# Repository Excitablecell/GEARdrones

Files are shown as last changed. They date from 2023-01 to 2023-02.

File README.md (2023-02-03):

# GEARdrones

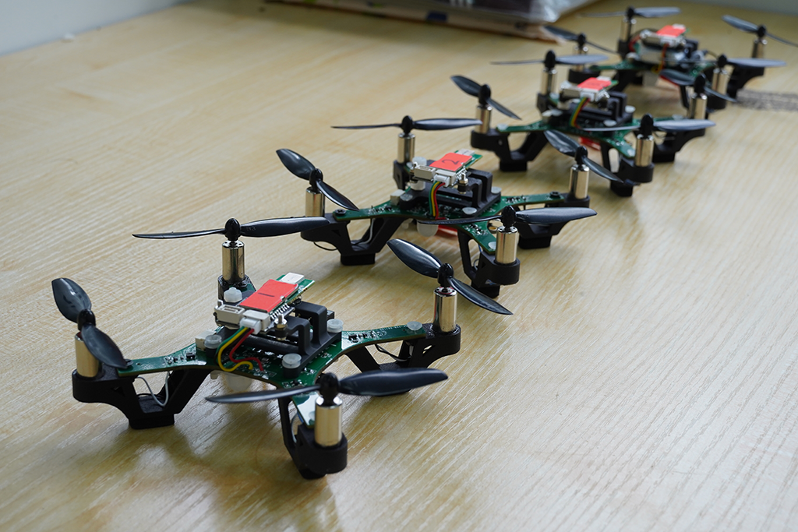
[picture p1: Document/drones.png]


> GEARdrones是一个专为**低成本无人机编队控制**所开发的，集**飞行控制器**、**UWB相对定位算法**、**软件上位机**于一体的四旋翼无人机系统。
>
> 演示视频：[自研无人机集群？理工男的大学生活也可以很精彩！](https://www.bilibili.com/video/BV1JY4y1o76U)
>
> 本项目主要包含以下内容：
>
> 	1.基于STM32F1和F4的两个版本的飞行控制器嵌入式软件工程
>
> 	2.基于STM32F1的遥控器嵌入式软件工程
>
> 	3.无人机的PCB工程(正在整理)、外壳模型
>
> 	4.相对定位算法的Matlab仿真文件
>
> 	5.基于PYQT5和MQTT开发的软件上位机

### 参考开发环境：

	嵌入式软件开发环境：Keil MDK5 5.29

	编译器：Arm Compiler V5.06 build750

	MQTT服务器：mosquito/EMQX

	MATLAB 2022B

	Python 3.8

### 参考文献：

> [1] Guo K, Xie L. INFRASTRUCTURE-FREE COOPERATIVE RELATIVE LOCALIZATION FOR UAVS IN GPS-DENIED ENVIRONMENTS[J]. International Journal of Robotics and Automation, 2021, 36(6).
>
> [2] Nguyen T M, Zaini A H, Guo K, et al. An ultra-wideband-based multi-UAV localization system in GPS-denied environments[C]//2016 International Micro Air Vehicles Conference. 2016, 6: 1-15.
>
> [3] Guo K, Qiu Z, Miao C, et al. Ultra-wideband-based localization for quadcopter navigation[J]. Unmanned Systems, 2016, 4(01): 23-34.
>
> [4] Guo K, Li X, Xie L. Ultra-wideband and odometry-based cooperative relative localization with application to multi-UAV formation control[J]. IEEE transactions on cybernetics, 2019, 50(6): 2590-2603.

### 参考开源库：

[SRML:华南虎嵌入式软件中间件层库](https://github.com/scutrobotlab/srml)

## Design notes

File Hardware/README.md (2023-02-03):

注意：PCB工程使用Altium Designer设计，使用其他EDA可能存在不兼容问题

所开源的PCB包含以下内容：

GEARdrones-Lite 原理图、PCB与BOM表

GEARdrones-F4 原理图、PCB

由于个人精力和开发周期的原因，F4版本的硬件方案仅用于测试分布式UWB相对定位算法，飞行功能没有被验证，本次开源也只是提供参考思路，具体原因可查阅：https://github.com/Excitablecell/GEARdrones/tree/main/Firmware

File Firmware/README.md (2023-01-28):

# GEARDRONE_LITE

GEARdrone for STM32F103

GEARdrone_Lite包含了完整的飞行控制器和机载UWB相对定位算法，可以在4基站模式下实现相对定位，或直接使用光流传感器进行定位悬停。

具体功能请查阅软件工程代码

# GEARDRONE_F4

 GEARdrone for STM32F411

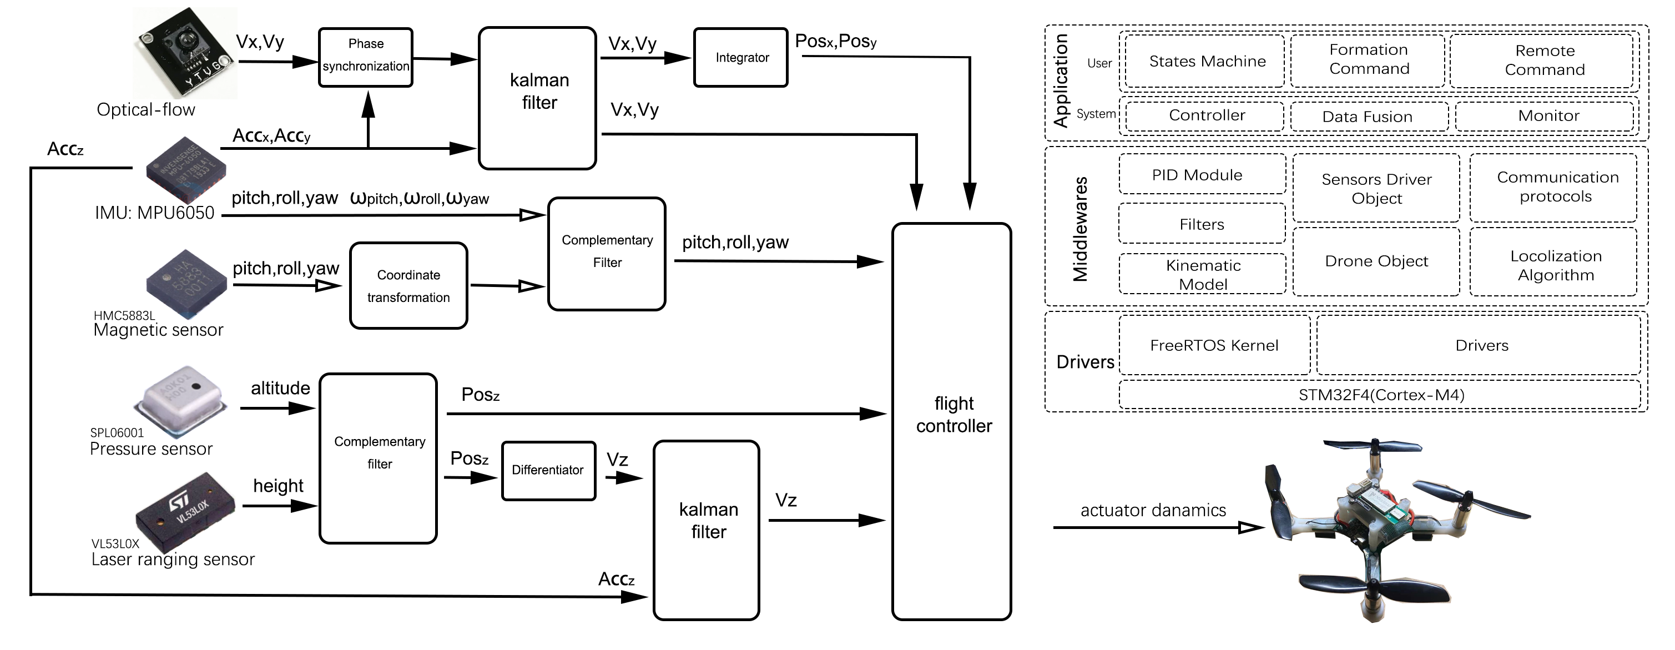
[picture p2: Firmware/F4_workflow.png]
F4 system workflow


F4版本飞控由于本人精力有限，在数次因layout问题打样测试失败后已暂停开发

值得参考的内容是 GEARdrone-F4\GearLL\Middlewares\Algorithm 目录下的 NLR_localization 文件

NLR_localization在单片机中实现非线性回归，复现了参考文献[1]中的第一部分无人机相对位置初始化部分的内容

完整论文复现的matlab仿真可以在software文件夹中查阅。

# GEARREMOTE

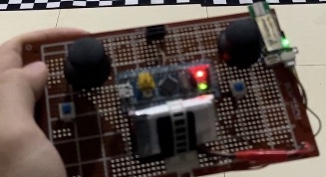
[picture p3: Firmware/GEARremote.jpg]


遥控器GEARremote原本是为了控制单独一架无人机设计的，使用串口透传模块进行通讯。但在后期编队开发中，为了下达广播起飞指令，遥控器摒弃了原先的设计，一直以面包板的形式支持无人机编队的开发，没有专门的PCB工程。

参考文献：

[1] Guo K, Xie L. INFRASTRUCTURE-FREE COOPERATIVE RELATIVE LOCALIZATION FOR UAVS IN GPS-DENIED ENVIRONMENTS[J]. International Journal of Robotics and Automation, 2021, 36(6).

[2] Nguyen T M, Zaini A H, Guo K, et al. An ultra-wideband-based multi-UAV localization system in GPS-denied environments[C]//2016 International Micro Air Vehicles Conference. 2016, 6: 1-15.

[3] Guo K, Qiu Z, Miao C, et al. Ultra-wideband-based localization for quadcopter navigation[J]. Unmanned Systems, 2016, 4(01): 23-34.

[4] Guo K, Li X, Xie L. Ultra-wideband and odometry-based cooperative relative localization with application to multi-UAV formation control[J]. IEEE transactions on cybernetics, 2019, 50(6): 2590-2603.

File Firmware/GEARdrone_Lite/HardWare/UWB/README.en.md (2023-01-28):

[简体中文](./README.md) | English

<h1 align="center">NLink Unpack</h1>

<div align="center">



NLink Unpack is used for products of Nooploop，like [LinkTrack](https://www.nooploop.com/)，[LinkTrack AOA](http://www.nooploop.com/linktrack-aoa)，[TOFSense](https://www.nooploop.com/tofsense.Written in pure C language, can be used for building protocol parsing code

 

</div>

## Notice

- In case of compilation errors, make sure the compiler has turned on C99 support
- NLink protocol data follows the Little-Endian mode, this example code runs in the mode too, and the Big-Endian mode is not supported
- For variable length protocols, such as NLink_LinkTrack_NodeFrame1, heap memory allocation is used for dynamic nodes. If there are many nodes, please ensure enough heap space

## Usage

Refer to [example.c](./example.c) to get start

## License

The source code is released under a [BSD 3-Clause license](LICENSE).

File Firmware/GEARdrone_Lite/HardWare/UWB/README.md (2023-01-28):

简体中文 | [English](./README.en.md) 

<h1 align="center">NLink Unpack</h1>

<div align="center">



NLink Unpack 用于支持Nooploop产品，如[LinkTrack](https://www.nooploop.com/)，[LinkTrack AOA](http://www.nooploop.com/linktrack-aoa)，[TOFSense](https://www.nooploop.com/tofsense)，纯C语言编写，用户可用于构建协议解析代码

 

</div>

## Notice
- 如编译错误，请确保编译器已经开启C99支持
- NLink协议数据遵循小端模式，本示例代码默认运行于小端模式，大端模式不可用
- 对于变长协议，如NLink_LinkTrack_NodeFrame1，动态节点部分采用了堆内存分配，如节点数量较多，请确保堆空间足够

## Usage

使用示例参考[example.c](./example.c)文件

## License

源码基于[BSD 3-Clause license](LICENSE)发布

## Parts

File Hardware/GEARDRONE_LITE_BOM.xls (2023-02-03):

型号 | 封装 | 位号 | 元件编号
0.22uf | 0603_C | C25 | C21120
22pF | C0603 | C10 | C1653
SS14 | SOD-323 | D4,D3,D2,D5,D1 | C699102
106 | C0603 | C5 | C96446
4.7uf | 0603_C | C24 | C19666
104 | C0603 | C14,C13,C7,C4,C16,C15,C3,C8,C6 | C14663
104 | 0603_C | C27,C26,C12,C11 | C14663
0.1uf | C0603 | C23,C22 | C14663
10nf | C0603 | C2 | C57112
10k | R0603 | R20,R19,R8,R6,R3,R33,R2,R1,R9 | C25804
10kΩ | R0603 | R10 | C25804
10k | 0603_R | R7,R11 | C25804
100k | R0603 | R30 | C25803
QMC5883L | LPCC-16_L3.0-W3.0-P0.50-BL | U4 | C976032
0 | R0603 | R5,R4 | C21189
SI2302 | LC-SOT-23(SOT-23-3) | Q5,Q4,Q3,Q2,Q1 | C2891732
73.2k | R0603 | R31 | C403343
5032 | SMD5032-2 | Y1 | C115962
STM32F103C8T6 | LC-LQFP-48_7X7X05P | U1 | C8734
4.7uH | CD43NP | L1 | C57269
2.2nf | C0603 | C1 | C1604
20pf | C0603 | C9 | C1648
SM04B-GHS-TB(LF)(SN) | CONN-SMD_4P-P1.25_SM04B-GHS-TB-LF-SN | U3 | C189895
EFD3-G9CA-P1WF | LED3528 | LED1 | C507038
SPL06-001 | SENSOR-SMD_SPL06-001 | U5 | C2684428
15pf | C0603 | C19 | C1644
ESP-12F(ESP8266MOD) | WIFIM-SMD_ESP-12F-ESP8266MOD | U2 | C82891
22uf | C0603 | C18,C17 | C59461
AMS1117-3.3 | LC-SOT-223 | T1 | C6186
SX1308 | LC-SOT-23-6 | IC2 | C78162
ECAP | TAN-A-3216 | C21,C20 | C7171

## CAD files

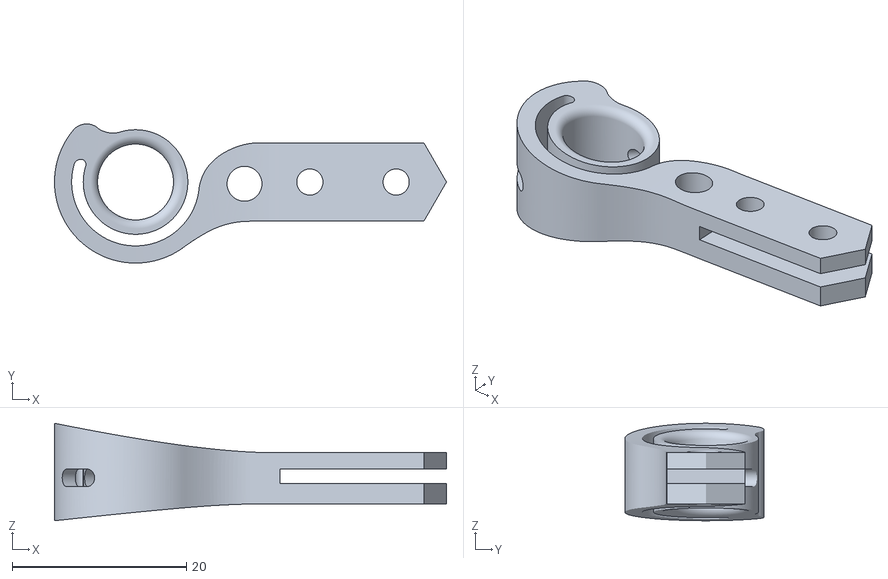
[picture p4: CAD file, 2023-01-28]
Model/GEARdrone_F4/Motor_holder_right.stl
45.0 x 16.0 x 11.2

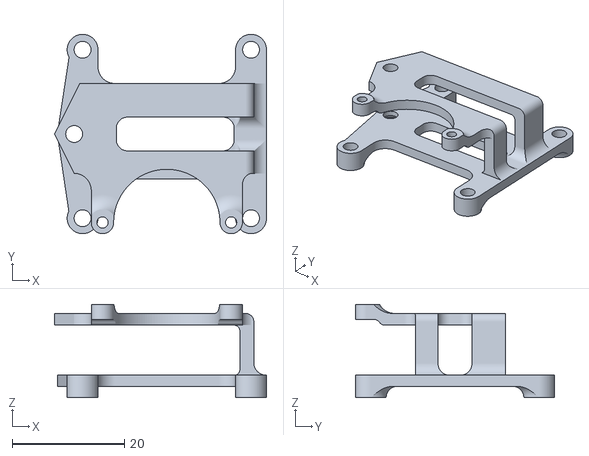
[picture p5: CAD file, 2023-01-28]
Model/GEARdrone_Lite/Upper_structure.stl
37.7 x 35.5 x 16.6

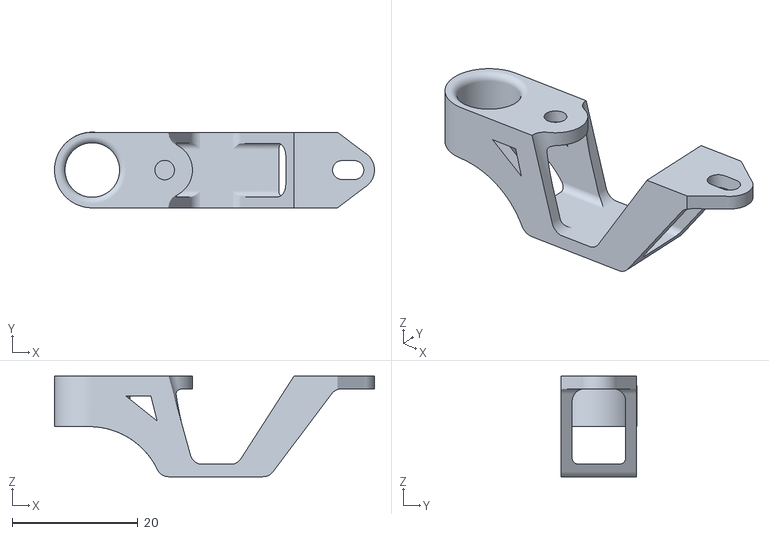
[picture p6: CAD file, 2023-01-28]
Model/GEARdrone_Lite/Motor_structure.stl
50.8 x 12.0 x 16.0

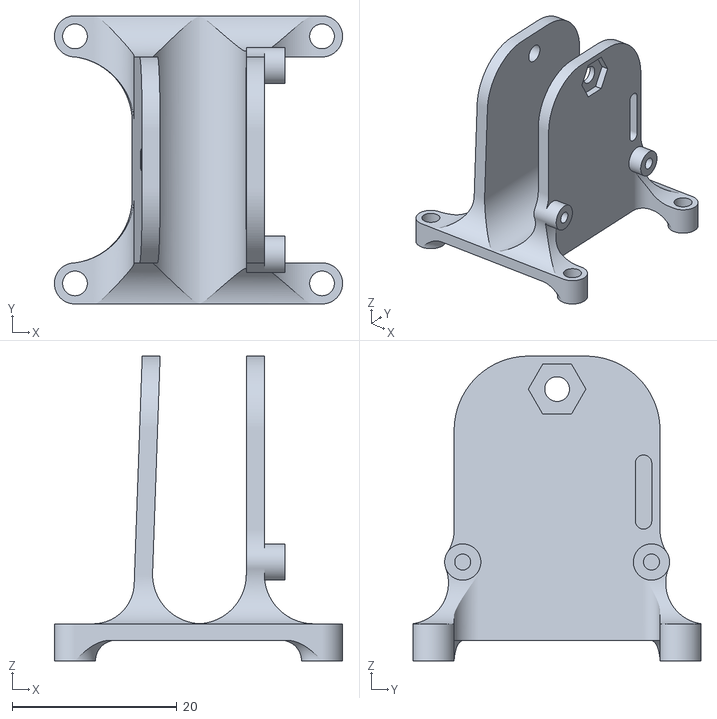
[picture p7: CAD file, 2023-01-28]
Model/GEARdrone_F4/Battery_holder.stl
35.0 x 35.0 x 37.0

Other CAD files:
Model/GEARdrone_F4/Motor_holder_left.stl

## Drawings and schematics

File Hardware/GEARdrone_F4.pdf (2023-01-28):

# stm32最小系统 MPU6050

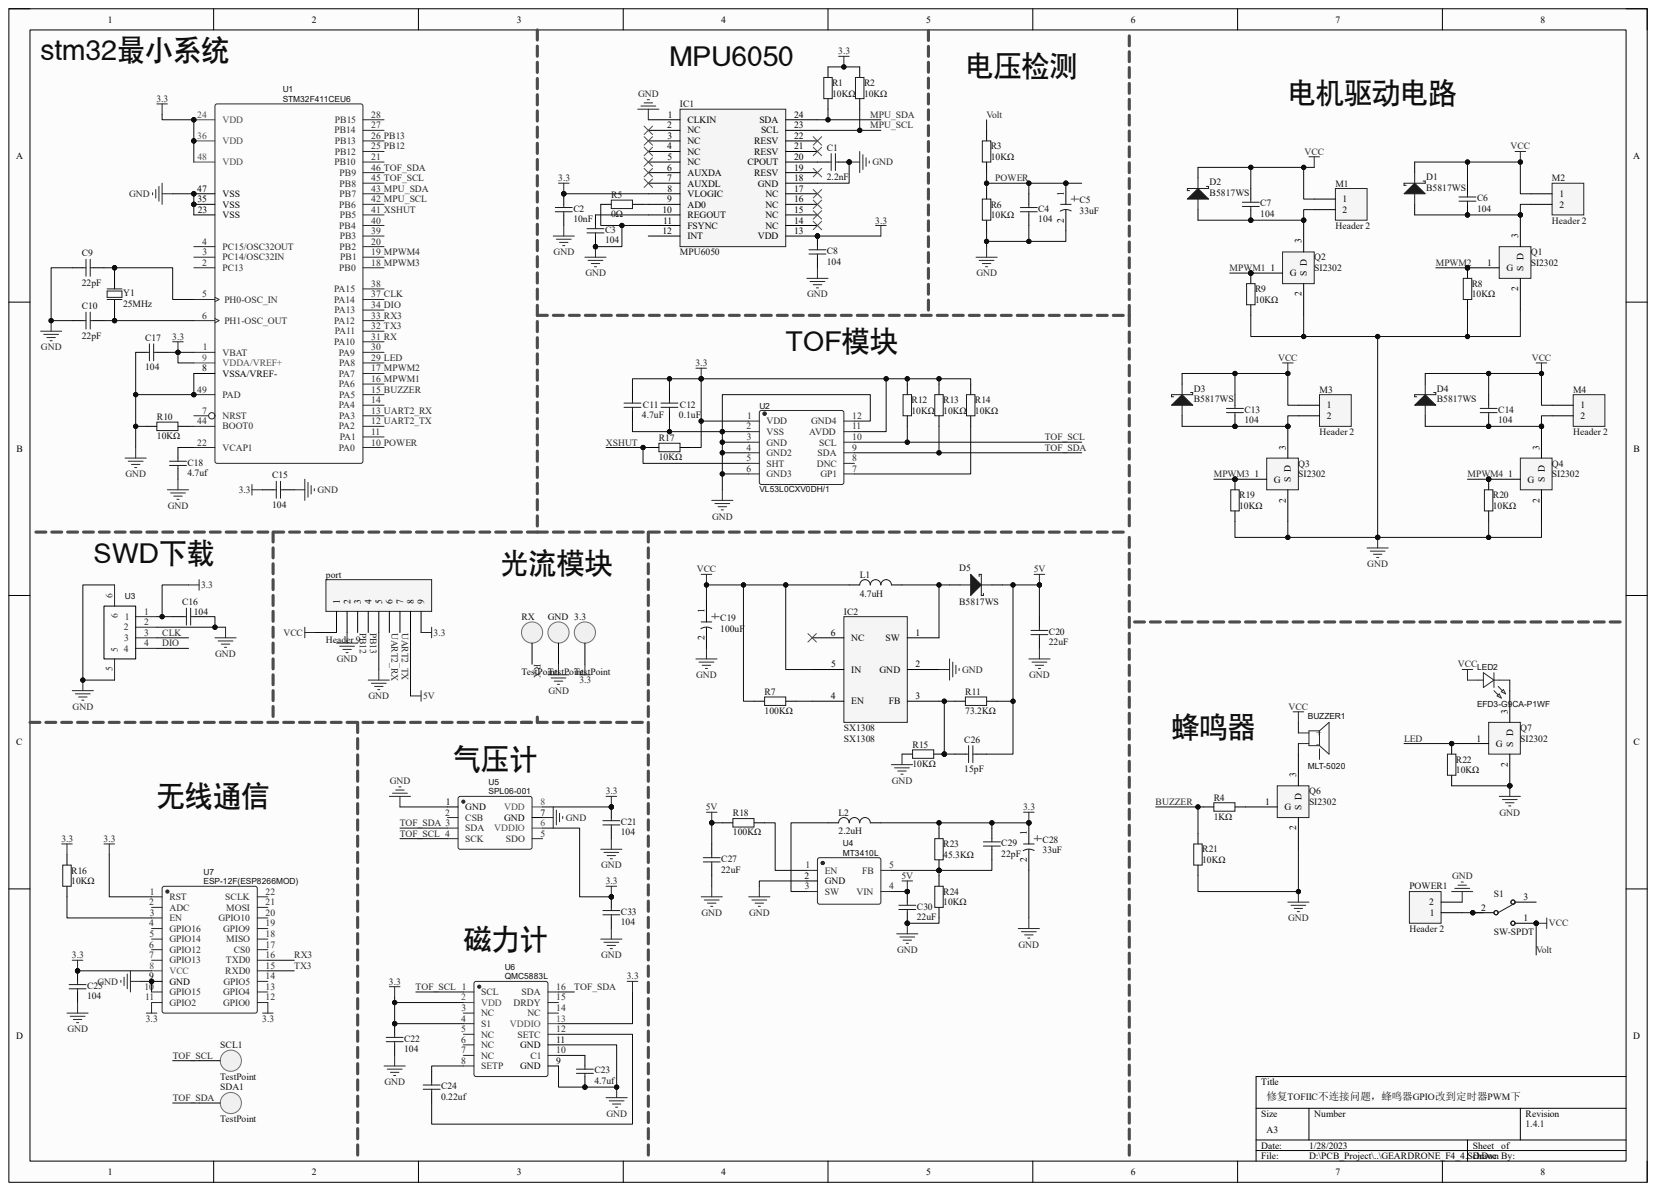
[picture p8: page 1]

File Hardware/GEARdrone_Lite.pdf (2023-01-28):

# stm32最小系统 MPU6050

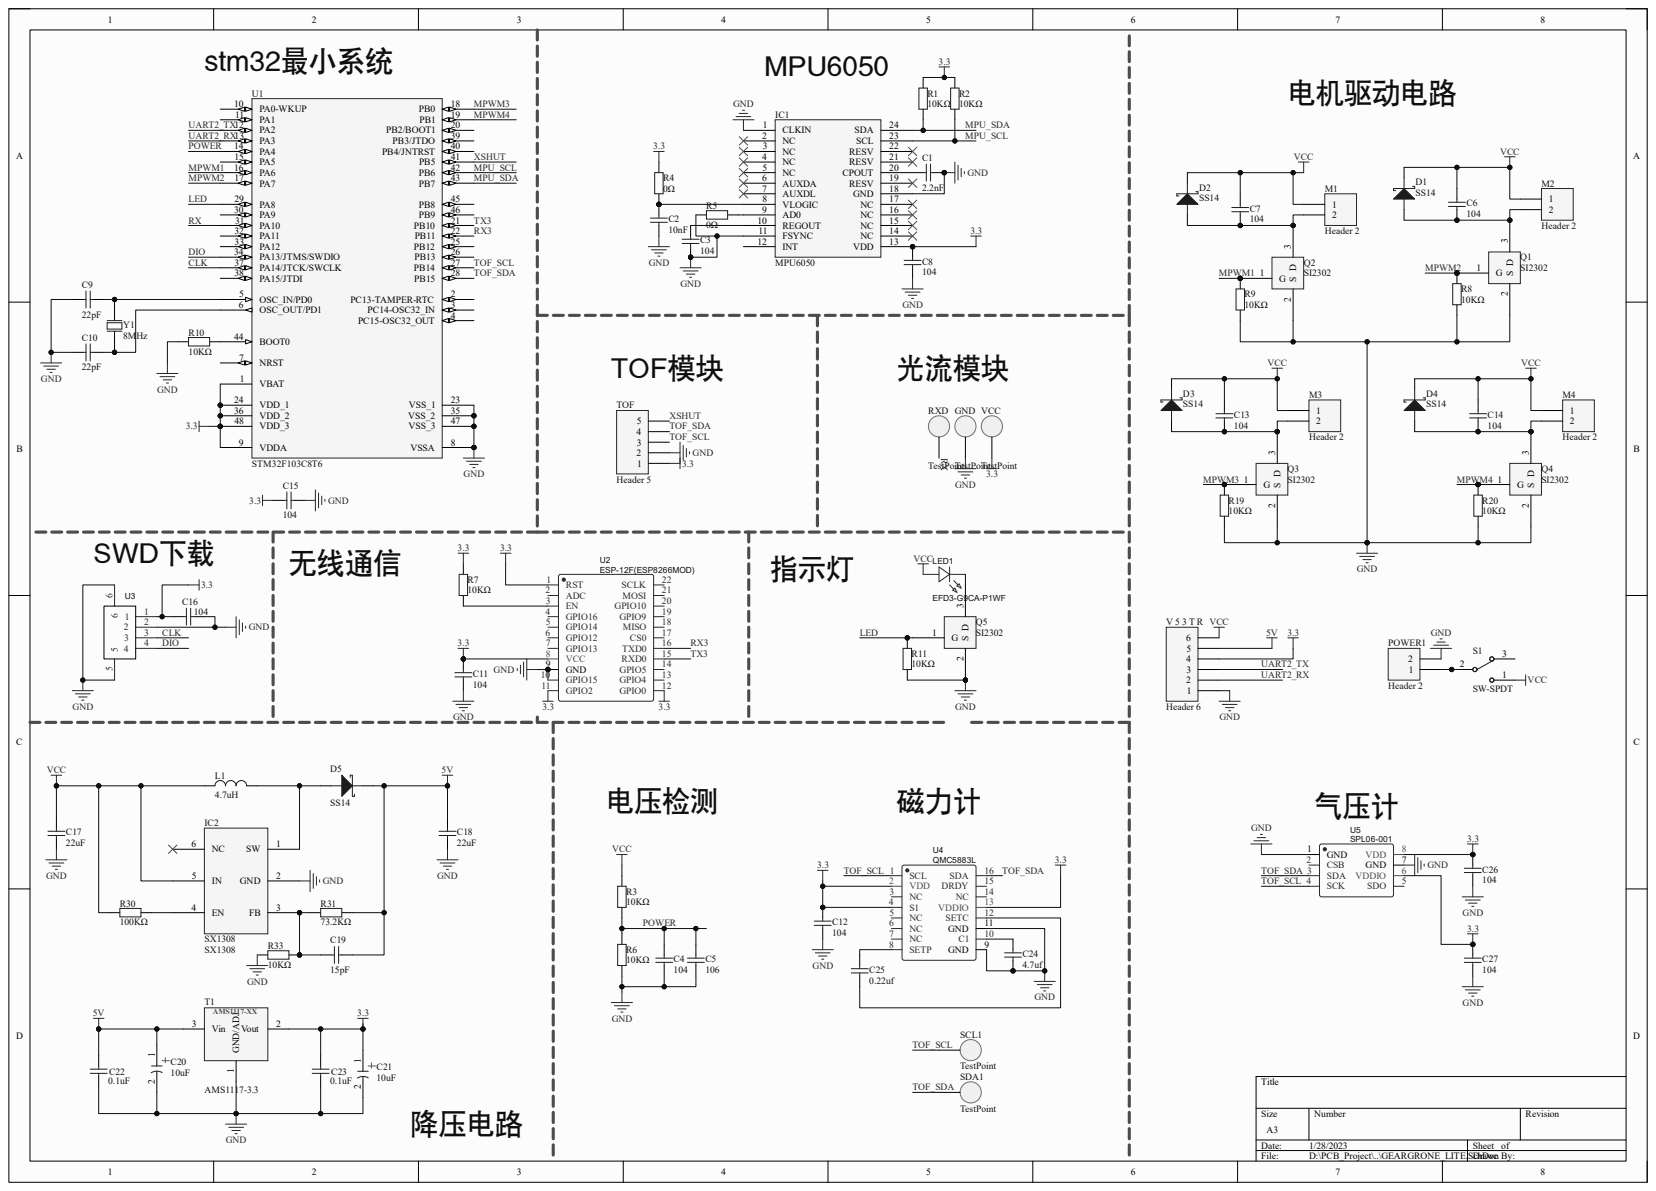
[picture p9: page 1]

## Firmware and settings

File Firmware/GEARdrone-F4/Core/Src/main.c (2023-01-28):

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
/* Includes ------------------------------------------------------------------*/
#include "main.h"
#include "cmsis_os.h"

/* USER CODE BEGIN Includes */
#include "SEGGER_SYSVIEW.h"
#include "inv_mpu.h"
#include "mpu6050.h"
#include "timer_driver.h"
/* USER CODE END Includes */

ADC_HandleTypeDef hadc1;
DMA_HandleTypeDef hdma_adc1;

I2C_HandleTypeDef hi2c1;

TIM_HandleTypeDef htim3;
TIM_HandleTypeDef htim4;
TIM_HandleTypeDef htim5;

UART_HandleTypeDef huart1;
UART_HandleTypeDef huart2;
UART_HandleTypeDef huart6;
DMA_HandleTypeDef hdma_usart1_rx;
DMA_HandleTypeDef hdma_usart1_tx;
DMA_HandleTypeDef hdma_usart2_tx;
DMA_HandleTypeDef hdma_usart2_rx;
DMA_HandleTypeDef hdma_usart6_rx;
DMA_HandleTypeDef hdma_usart6_tx;

osThreadId defaultTaskHandle;
void SystemClock_Config(void);
static void MX_GPIO_Init(void);
static void MX_DMA_Init(void);
static void MX_ADC1_Init(void);
static void MX_TIM3_Init(void);
static void MX_USART1_UART_Init(void);
static void MX_USART2_UART_Init(void);
static void MX_USART6_UART_Init(void);
static void MX_TIM4_Init(void);
static void MX_TIM5_Init(void);
static void MX_I2C1_Init(void);
void StartDefaultTask(void const * argument);

/* USER CODE BEGIN 0 */
#pragma import(__use_no_semihosting)
//标准库需要的支持函数
struct __FILE 
{
  int handle; 
};

FILE __stdout;
//定义_sys_exit()以避免使用半主机模式  
void _sys_exit(int x){x = x;}
void _ttywrch(int ch){ch = ch;}
	
//重定义fputc函数
int fputc(int ch, FILE *f){
  HAL_UART_Transmit(&huart6, (uint8_t *)&ch,1,0xff);  //根据使用的库重定向
  return ch;
}
uint8_t _dbg_TXBuff[20];
void uart2_printf(const char *format,...)
{
	uint32_t length;
	va_list args;

	va_start(args, format);
	length = vsnprintf((char*)_dbg_TXBuff, sizeof(_dbg_TXBuff)+1, (char*)format, args);
	va_end(args);
	HAL_UART_Transmit(&huart2,_dbg_TXBuff,length,0xff);
}
/* USER CODE END 0 */

/**
  * @brief  The application entry point.
  * @retval int
  */
int main(void)
{
  /* MCU Configuration--------------------------------------------------------*/

  /* Reset of all peripherals, Initializes the Flash interface and the Systick. */
  HAL_Init();

  /* Configure the system clock */
  SystemClock_Config();

  /* Initialize all configured peripherals */
  MX_GPIO_Init();
  MX_DMA_Init();
  MX_ADC1_Init();
  MX_TIM3_Init();
  MX_USART1_UART_Init();
  MX_USART2_UART_Init();
  MX_USART6_UART_Init();
  MX_TIM4_Init();
  MX_TIM5_Init();
  MX_I2C1_Init();
  /* USER CODE BEGIN 2 */
	System_Task_Init();
	SEGGER_SYSVIEW_Conf();
  /* USER CODE END 2 */

  /* USER CODE BEGIN RTOS_MUTEX */
  /* add mutexes, ... */
  /* USER CODE END RTOS_MUTEX */

  /* USER CODE BEGIN RTOS_SEMAPHORES */
  /* add semaphores, ... */
  /* USER CODE END RTOS_SEMAPHORES */

  /* USER CODE BEGIN RTOS_TIMERS */
  /* start timers, add new ones, ... */
  /* USER CODE END RTOS_TIMERS */

  /* USER CODE BEGIN RTOS_QUEUES */
  /* add queues, ... */
  /* USER CODE END RTOS_QUEUES */

  /* Create the thread(s) */
  /* definition and creation of defaultTask */
  osThreadDef(defaultTask, StartDefaultTask, osPriorityNormal, 0, 128);
  defaultTaskHandle = osThreadCreate(osThread(defaultTask), NULL);

  /* USER CODE BEGIN RTOS_THREADS */
  /* add threads, ... */
  /* USER CODE END RTOS_THREADS */

  /* Start scheduler */
  osKernelStart();

  /* We should never get here as control is now taken by the scheduler */
  /* Infinite loop */
  /* USER CODE BEGIN WHILE */
  while (1)
  {
    /* USER CODE END WHILE */

    /* USER CODE BEGIN 3 */
  }
  /* USER CODE END 3 */
}

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
/* USER CODE BEGIN Header_StartDefaultTask */
/**
  * @brief  Function implementing the defaultTask thread.
  * @param  argument: Not used
  * @retval None
  */
/* USER CODE END Header_StartDefaultTask */
void StartDefaultTask(void const * argument)
{
  /* USER CODE BEGIN 5 */
  /* Infinite loop */
  for(;;)
  {
		System_time_us = Get_SystemTimer();
    osDelay(1);

  }
  /* USER CODE END 5 */
}

/**
  * @brief  Period elapsed callback in non blocking mode
  * @note   This function is called  when TIM11 interrupt took place, inside
  * HAL_TIM_IRQHandler(). It makes a direct call to HAL_IncTick() to increment
  * a global variable "uwTick" used as application time base.
  * @param  htim : TIM handle
  * @retval None
  */
void HAL_TIM_PeriodElapsedCallback(TIM_HandleTypeDef *htim)
{
  /* USER CODE BEGIN Callback 0 */
	if (htim->Instance == TIM5) {
    Update_SystemTick();
  }
  /* USER CODE END Callback 0 */
  if (htim->Instance == TIM11) {
    HAL_IncTick();
  }
}

/**
  * @brief  This function is executed in case of error occurrence.
  * @retval None
  */
void Error_Handler(void)
{
  /* USER CODE BEGIN Error_Handler_Debug */
  /* User can add his own implementation to report the HAL error return state */
  __disable_irq();
  while (1)
  {
  }
  /* USER CODE END Error_Handler_Debug */
}

#ifdef  USE_FULL_ASSERT
/**
  * @brief  Reports the name of the source file and the source line number
  *         where the assert_param error has occurred.
  * @param  file: pointer to the source file name
  * @param  line: assert_param error line source number
  * @retval None
  */
void assert_failed(uint8_t *file, uint32_t line)
{
  /* USER CODE BEGIN 6 */
  /* User can add his own implementation to report the file name and line number,
     ex: printf("Wrong parameters value: file %s on line %d\r\n", file, line) */
  /* USER CODE END 6 */
}
#endif /* USE_FULL_ASSERT */

/************************ (C) COPYRIGHT STMicroelectronics *****END OF FILE****/

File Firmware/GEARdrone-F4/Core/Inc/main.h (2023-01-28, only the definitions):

#define ESPEN_Pin GPIO_PIN_12
#define ESPEN_GPIO_Port GPIOB
#define BEEP_Pin GPIO_PIN_15
#define BEEP_GPIO_Port GPIOB
#define LED_Pin GPIO_PIN_8
#define LED_GPIO_Port GPIOA
#define XSHUT_Pin GPIO_PIN_5
#define XSHUT_GPIO_Port GPIOB
#define TOF_SCL_Pin GPIO_PIN_8
#define TOF_SCL_GPIO_Port GPIOB
#define TOF_SDA_Pin GPIO_PIN_9
#define TOF_SDA_GPIO_Port GPIOB

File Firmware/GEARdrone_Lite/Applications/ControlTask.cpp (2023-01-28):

/********************************************************************************
  * Copyright (c) 2022 - ~, EXcai(亢体造梦)
  * @author  EXcai
  * @brief   无人机状态机
  *
  ==============================================================================
													 该文件包含以下内容
  ==============================================================================
    @note
			-无人机异常状态监控（低压、倾角过大、传感器故障等）
			-简易的无人机状态机
			-无人机状态调度任务

  	@warning 
			- Standard C++11 required! 
	******************************************************************************
  * @attention
  * 
  * if you had modified this file, please make sure your code does not have many 
  * bugs, update the version Number, write dowm your name and the date, the most
  * important is make sure the users will have clear and definite understanding 
  * through your new brief.
  *

  ********************************************************************************/

#include "Drone.h"

GearDrone Drone;
Mpu6050_Data Mpu6050;
extern UWB Uwb;
extern int volt[2];

/*光流数据处理*/
extern uint8_t optic_flow[9];
extern uint8_t data[100];

extern uint8_t remote_command;
MeanFilter<5> Power;
/********************************************************************************
 * @brief  	无人机异常状态监控
 
 * @param  	时刻准备进入异常模式
 
 * @retval 	
 * @author	EXcai(亢体造梦)
 *******************************************************************************/
uint8_t GearDrone::Error_Monitor (uint8_t drone_state){
	
	if(Error_Code != 0){
		Drone_Mode = 5;
		drone_state = 0;
		return drone_state;
	}
	
	if(battery_voltage[1] < 375){
		Drone.Init_PWM = 0;
		Error_Code = 2;//low power
		drone_state = 0;
		HAL_GPIO_WritePin(LED_GPIO_Port,LED_Pin,GPIO_PIN_RESET);//电池电量低，关灯
		return drone_state;
	}
	if(fabsf(pitch) > 40 || pitch == 0){
		Error_Code = 3;//out of angle limit
		drone_state = 0;
		return drone_state;
	}
	if(fabsf(roll) > 40 || roll == 0){
		Error_Code = 3;//out of angle limit
		drone_state = 0;
		return drone_state;
	}
	if(Drone.z_pos > 2.6){
		Drone.Init_PWM = 0;
		Error_Code = 5;//超过限高
		drone_state = 0;
		return drone_state;
	}
	if(optic_flow[0] == 0){
		Error_Code = 6;//optical flow error
		drone_state = 0;
		return drone_state;
	}
	if(VL53.comms_type != 1){
		Error_Code = 7;//tof error
		drone_state = 0;
		return drone_state;
	}
	
	if(Mpu6050.mpu_status != 0){//mpu error
		Mpu6050.mpu_error_count++;
	}
	else{
		Mpu6050.mpu_error_count = 0;
	}
	if(Mpu6050.mpu_error_count > 4){
		Error_Code = 8;//mpu error
		drone_state = 0;
		return drone_state;
	}
	
	#if USE_UWB
	Uwb.time_span = (Drone.systemtime_10ms - Uwb.system_time)/10.0f;
	if(Uwb.time_span > 10){
		Error_Code = 9;//uwb offline
		drone_state = 0;
		return drone_state;
	}
	#endif
	
	if(remote_command == 3){
		Error_Code = 12;// manual crash
	}
	
	return drone_state;
}
/********************************************************************************
 * @brief  	无人机启动 0
 
 * @param  	Startup()以初始化无人机，
 
 * @retval 	0: mode
						1: mode
						5: mode
 * @author	EXcai(亢体造梦)
 *******************************************************************************/
uint8_t GearDrone::Startup(uint8_t mode){
	
	if(systemtime_10ms == 100){printf_dma(&huart3,"ATE0\r\n");}
	if(systemtime_10ms == 150){printf_dma(&huart3,"AT+CWMODE=1\r\n");}
	if(systemtime_10ms == 200){printf_dma(&huart3,"AT+CWJAP=\"GEAR\",\"geardrone\"\r\n");}
	#if NETWORK_PROTOCOL
	if(systemtime_10ms == 300){printf_dma(&huart3,"AT+MQTTUSERCFG=0,1,\"MAV%u\",\"admin\",\"public\",0,0,\"\"\r\n",Uwb.id);}
	if(systemtime_10ms == 350){printf_dma(&huart3,"AT+MQTTCONN=0,\"192.168.0.120\",1883,0\r\n");}
	if(systemtime_10ms == 600){printf_dma(&huart3,"ATE0\r\n");}
	if(systemtime_10ms == 700){printf_dma(&huart3,"AT+MQTTSUB=0,\"%s\",0\r\n","Remote");}
	if(systemtime_10ms == 750){printf_dma(&huart3,"AT+MQTTSUB=0,\"%s\",0\r\n","MATLAB");}
	if(systemtime_10ms == 800){printf_dma(&huart3,"AT+MQTTSUB=0,\"MAV%u_RX\",0\r\n",Uwb.id);memset(data,0,100);}
	#else
	if(systemtime_10ms == 350){printf("AT+CIPSTART=\"UDP\",\"255.255.255.255\",12138,100%u\r\n",Uwb.id);}
	if(systemtime_10ms == 450){printf("AT+CIPMODE=1\r\n");}
	if(systemtime_10ms == 550){printf("AT+CIPSEND\r\n");}
	#endif
	if(systemtime_10ms < 800){
		battery_voltage[1] = battery_voltage[0];
		Mpu6050.x_speed_mpu = 0;
		Mpu6050.y_speed_mpu = 0;
		Mpu6050.z_speed_mpu = 0;
		yaw_init = yaw;
	}
	if(systemtime_10ms > 800 && Controller_State == 0){
		Controller_State = 1;
		mode = 1;
		HAL_GPIO_WritePin(LED_GPIO_Port,LED_Pin,GPIO_PIN_SET);//LED on
		target_x_pos = init_x_pos;
		target_y_pos = init_y_pos;
	}
	return mode;
}
/********************************************************************************
 * @brief  	无人机起飞状态 1
 
 * @param  	无人机起飞状态
 
 * @author	EXcai(亢体造梦)
 *******************************************************************************/
uint8_t GearDrone::Taskoff_State(uint8_t mode){
	
	if(Error_Code == 0 && remote_command == 2){Controller_State = 1;remote_command = 0;}
	
	if(Controller_State == 1){
			if(remote_command == 1){
				/*逐渐提升转速以起飞*/
				target_z_pos = 0.4f;
				if(z_pos < 0.095 && Init_PWM < 9500){
					if(Init_PWM < 4000){Init_PWM = 8100;}
					Init_PWM += 10;
				}
				else{
					mode = 2;
				}
				PID_position_controller(Controller_State);
			}
			else{
				#if DISABLE_MOTORS //电机不要转动
				__HAL_TIM_SET_COMPARE(&htim3, TIM_CHANNEL_2,0);//lb
				__HAL_TIM_SET_COMPARE(&htim3, TIM_CHANNEL_1,0);//rb
				__HAL_TIM_SET_COMPARE(&htim3, TIM_CHANNEL_4,0);//lf
				__HAL_TIM_SET_COMPARE(&htim3, TIM_CHANNEL_3,0);//rf
				#else
				__HAL_TIM_SET_COMPARE(&htim3, TIM_CHANNEL_2,Init_PWM);//lb
				__HAL_TIM_SET_COMPARE(&htim3, TIM_CHANNEL_1,Init_PWM);//rb
				__HAL_TIM_SET_COMPARE(&htim3, TIM_CHANNEL_4,Init_PWM);//lf
				__HAL_TIM_SET_COMPARE(&htim3, TIM_CHANNEL_3,Init_PWM);//rf
				#endif
			}
		}
		else{
			mode = 5;
			Error_Code = 11;
		}
		return mode;
}
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

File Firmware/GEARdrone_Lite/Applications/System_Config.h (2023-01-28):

/********************************************************************************
  * Copyright (c) 2022 - ~, EXcai(亢体造梦)
  * @file    System_Config.h
  * @author  EXcai(亢体造梦)
  * @brief   配置文件，用于在软硬件不同方案间切换
  *
  *******************************************************************************/
#pragma once

#ifndef __SYSTEM_CONFIG_H__
#define __SYSTEM_CONFIG_H__

/*********************************************************************************
	* @brief  电机停转(用于测试各个功能是否正常)
	* @param  -1:电机不要转动
						-0:电机可以转动

	* @author EXcai亢体造梦
	********************************************************************************/
#define DISABLE_MOTORS 0

/*********************************************************************************
	* @brief  使用UWB定位，确保UWB基站已部署并标定！
	* @param  -1:使用UWB提供位置，速度
						-0:使用光流传感器提供位置，速度

	* @author EXcai亢体造梦
	********************************************************************************/
#define USE_UWB 0

#define LP_Mode 0 //uwb局部定位模式
#define DR_Mode 1 //uwb测距模式

/*********************************************************************************
	* @brief  使用磁力计
	* @param  -1:使用磁力计
						-0:不使用磁力计
						
	* @note		在目前版本的PCB上，电机一转这玩意的数值就会飞。

	* @author EXcai亢体造梦
	********************************************************************************/
#define USE_MAGSENSOR 0

/*********************************************************************************
	* @brief  使用气压计
	* @param  -1:使用气压计
						-0:不使用气压计
						
	* @note		气压计要做好海绵包裹！！防止桨叶气流扰动影响采样！！！

	* @author EXcai亢体造梦
	********************************************************************************/
#define USE_BAROMETER 0 

/*********************************************************************************
	* @brief  使用matlab进行远程二阶控制
	* @param  -1:使用matlab二阶控制

	* @author EXcai亢体造梦
	********************************************************************************/
#define MATLAB_SECOND_OREDER_CONTROL 0

/*********************************************************************************
	* @brief  切换控制器
	* @param  -1:输出调节位置控制(未完成)
						-0:PID位置控制

	* @author EXcai亢体造梦
	********************************************************************************/
#define OUTPUT_REGULATION_CONTROLLER 0

/*********************************************************************************
	* @brief  使能机内绕圆
	* @param  -1:生成并使用机内绕圆轨迹

	* @author EXcai亢体造梦
	********************************************************************************/
#define RUN_CIRCLE_PATH 0
#define RADIUS 2.0 //半径
#define T 0.01 //周期
#define WR 0.4 //角速度

#define CENTER_X_POS -5 //圆心x位置
#define CENTER_Y_POS 5 //圆心y位置

/*********************************************************************************
	* @brief  使能缓慢上升
	* @param  -1:使无人机从0.4m向更高高度缓慢爬升

	* @author EXcai亢体造梦
	********************************************************************************/
#define DYNAMIC_HEIGHT 1

#define HEIGHT_TARGET 0.6f

/*********************************************************************************
* @brief  切换传输数据的网络协议
	* @param  -0:使用UDP传输数据(对应远端GEARmonitor_UDP.py)
						-1:使用MQTT协议传输数据(对应远端GEARmonitor_MQTT.py runn.m monitor2.m)

	* @author EXcai亢体造梦
	********************************************************************************/
#define NETWORK_PROTOCOL 1
#define MQTT_TEMPLATE "AT+MQTTPUB=0,\"MAV%u_TX\",\"{\\\"type\\\":1\\,\\\"time\\\":%u\\,\\\"value1\\\":%.3f\\,\\\"value2\\\":%.3f\\,\\\"value3\\\":%.3f}\",1,0\r\n"
#define MQTT_TEMPLATE_FLOAT "AT+MQTTPUB=0,\"MAV%u_TX\",\"{\\\"type\\\":1\\,\\\"time\\\":%.3f\\,\\\"value1\\\":%.3f\\,\\\"value2\\\":%.3f\\,\\\"value3\\\":%.3f}\",1,0\r\n"

/*********************************************************************************
* @brief  发送格式
	* @param  -0:GEARmonitor
						-1:matlab 单机
						-2:matlab 多机
						-3:uwb 多机机间通信

	* @author EXcai亢体造梦
	********************************************************************************/
#define SEND_TYPE 5

/*********************************************************************************
* @brief  切换红外测距芯片方案
	* @param  -0:VL53L0X
						-1:VL53L1

	* @author EXcai亢体造梦
	********************************************************************************/
#define TOF_SENSOR 1

#endif

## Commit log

2023-01-28 修改README
2023-01-28 修订readme
2023-02-03 更新上传硬件方案
    [GEARDRONE_F4_4.SchDoc, GEARDRONE_LITE.SchDoc, GEARDRONE_LITE_BOM.xls]

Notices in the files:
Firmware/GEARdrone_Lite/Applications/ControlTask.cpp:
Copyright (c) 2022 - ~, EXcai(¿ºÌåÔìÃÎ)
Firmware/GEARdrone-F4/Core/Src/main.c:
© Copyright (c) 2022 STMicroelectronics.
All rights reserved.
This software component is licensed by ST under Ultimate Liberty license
